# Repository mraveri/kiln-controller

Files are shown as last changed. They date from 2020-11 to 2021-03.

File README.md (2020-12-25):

Kiln Controller
==========

Turns a Raspberry Pi into an inexpensive, web-enabled kiln controller.

## Features

  * easy to create new kiln schedules and edit / modify existing schedules
  * no limit to runtime - fire for days if you want
  * view status from multiple devices at once - computer, tablet etc
  * firing cost estimate
  * NIST-linearized conversion for accurate K type thermocouple readings
  * supports PID parameters you tune to your kiln
  * monitors temperature in kiln after schedule has ended
  * api for starting and stopping at any point in a schedule

**Run Kiln Schedule**



**Edit Kiln Schedule**



## Hardware

### Parts

| Image | Hardware | Description |
| ---| --- | --- |
|  | [Raspberry Pi](https://www.adafruit.com/category/105) | Virtually any Raspberry Pi will work since only a few GPIO pins are being used. |
|  | [MAX 31855](https://www.adafruit.com/product/269) | Thermocouple breakout board |
|  | [K-Type Thermocouple](https://www.auberins.com/index.php?main_page=product_info&cPath=20_3&products_id=39) | Invest in a heavy duty, ceramic, k-type thermocouple designed for kilns |
|  | Breadboard | breadboard, ribbon cable, connector for pi's gpio pins & connecting wires |
|  | Solid State Relay | Zero crossing, make sure it can handle the max current of your kiln. Even if the kiln is 220V you can buy a single [3 Phase SSR](https://www.auberins.com/index.php?main_page=product_info&cPath=2_30&products_id=331). It's like having 3 SSRs in one.  Relays this big always require a heat sink. |
|  | Electric Kiln | There are many old electric kilns on the market that don't have digital controls. You can pick one up on the used market cheaply.  This controller will work with 110V or 220V (pick a proper SSR). My kiln is a Skutt KS-1018. |

### Schematic

The pi has three gpio pins connected to the MAX31855 chip. D0 is configured as an input and CS and CLK are outputs. The signal that controls the solid state relay starts as a gpio output which drives a transistor acting as a switch in front of it. This transistor provides 5V and plenty of current to control the ssr. Since only four gpio pins are in use, any pi can be used for this project. See the [config](https://github.com/jbruce12000/kiln-controller/blob/master/config.py) file for gpio pin configuration.

My controller plugs into the wall, and the kiln plugs into the controller.

**WARNING** This project involves high voltages and high currents. Please make sure that anything you build conforms to local electrical codes and aligns with industry best practices.



*Note: I tried to power my ssr directly using a gpio pin, but it did not work. My ssr required 25ma to switch and rpi's gpio could only provide 16ma. YMMV.*

## Software

### Raspbian

Download [NOOBs](https://www.raspberrypi.org/downloads/noobs/). Copy files to an SD card. Install raspbian on RPi using NOOBs.

    $ sudo apt-get install python3-pip python3-dev python3-virtualenv libevent-dev virtualenv
    $ git clone https://github.com/jbruce12000/kiln-controller.git
    $ cd kiln-controller
    $ virtualenv -p python3 venv
    $ source venv/bin/activate
    $ pip install --upgrade setuptools
    $ pip install greenlet bottle gevent gevent-websocket

*Note: The above steps work on ubuntu if you prefer*

### Raspberry PI deployment

If you want to deploy the code on a PI for production:

    $ cd kiln-controller
    $ virtualenv -p python3 venv
    $ source venv/bin/activate
    $ pip install RPi.GPIO

If you also want to use the in-kernel SPI drivers with a MAX31855 sensor:

    $ sudo apt-get install python-dev
    $ pip install Adafruit-MAX31855

## Configuration

All parameters are defined in config.py, just copy the example and review/change to your mind's content.

    $ cp config.py.EXAMPLE config.py

You should change, test, and verify PID parameters in config.py.  Here is a [PID Tuning Guide](https://github.com/jbruce12000/kiln-controller/blob/master/docs/pid_tuning.md).

You may want to change the configuration parameter **sensor_time_wait**. It's the duty cycle for the entire system.  It's set to two seconds by default which means that a decision is made every 2s about whether to turn on relay[s] and for how long. If you use mechanical relays, you may want to increase this. At 2s, my SSR switches 11,000 times in 13 hours.

## Usage

### Server Startup

    $ source venv/bin/activate; ./kiln-controller.py

### Autostart Server onBoot
If you want the server to autostart on boot, run the following commands

    $ /home/pi/kiln-controller/start-on-boot

### Client Access

Click http://127.0.0.1:8081 for local development or the IP
of your PI and the port defined in config.py (default 8081).

### Simulation

Select a profile and click Start. If you do not have a raspberry pi connected
and configured, then your run will be simulated.  Simulations run at near real
time and kiln characteristics are defined in config.py.

## License

This program is free software: you can redistribute it and/or modify
it under the terms of the GNU General Public License as published by
the Free Software Foundation, either version 3 of the License, or
(at your option) any later version.

This program is distributed in the hope that it will be useful,
but WITHOUT ANY WARRANTY; without even the implied warranty of
MERCHANTABILITY or FITNESS FOR A PARTICULAR PURPOSE.  See the
GNU General Public License for more details.

You should have received a copy of the GNU General Public License
along with this program.  If not, see <http://www.gnu.org/licenses/>.

## Support & Contact

Please use the issue tracker for project related issues.
If you're having trouble with hardware, I did too.  Here is a [troubleshooting guide](https://github.com/jbruce12000/kiln-controller/blob/master/docs/troubleshooting.md) I created for testing RPi gpio pins.

## Origin
This project was originally forked from https://github.com/apollo-ng/picoReflow but has diverged a large amount.

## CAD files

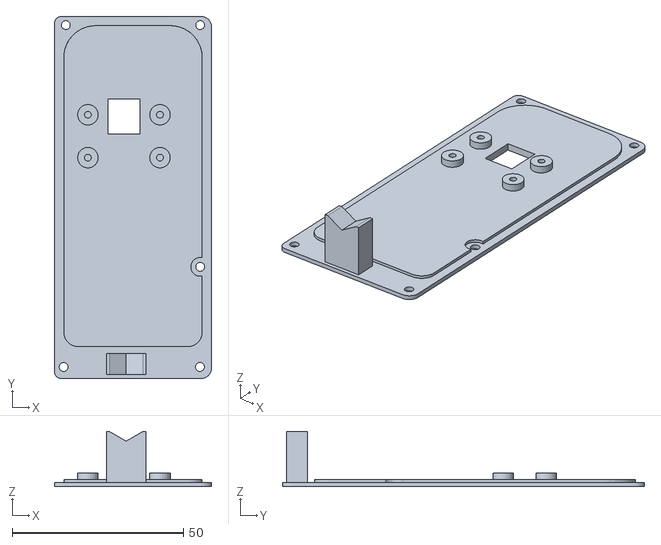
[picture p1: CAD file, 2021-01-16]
3d_model/box A.stl
45.8 x 105.7 x 16.1

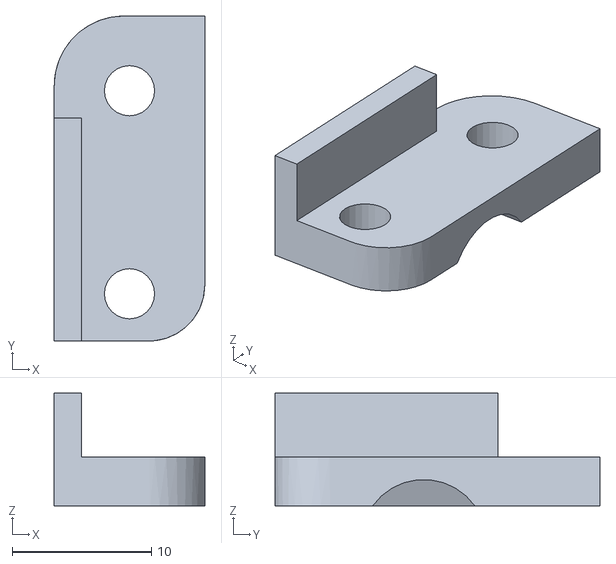
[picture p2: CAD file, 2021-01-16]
3d_model/box C.stl
10.8 x 23.3 x 8.09

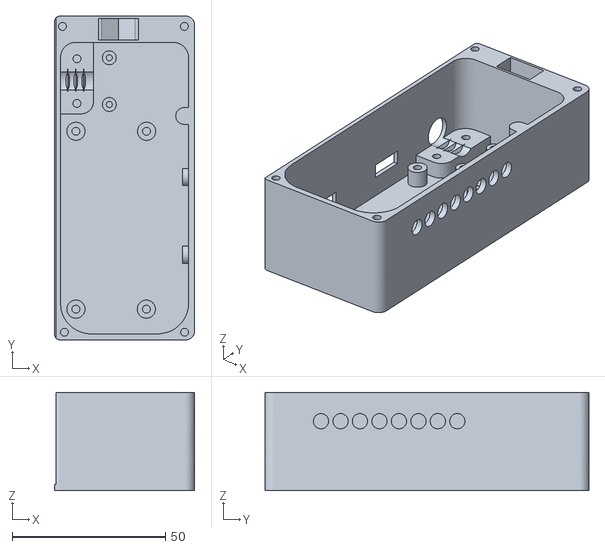
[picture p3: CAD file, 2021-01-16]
3d_model/box B.stl
45.8 x 105.7 x 32.0

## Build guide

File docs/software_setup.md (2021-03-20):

Kiln Monitor Software Set-up
============================

These instructions work for a headless set up that requires no external monitor but intensive command line work. It should be possible to do most of this with a monitor as well but I have not tried.

## General set-up

This part takes care of setting up the Raspberry and the OS. Each of this steps should have infinite tutorials online if needed.

In particular I use mac-os and I'll write commands for that. This should be morally similar for linux but definitely not for windows.

Main reference is this page:

    https://www.raspberrypi.org/documentation/configuration/wireless/headless.md

Start by burning the Raspbian image to an SD card.

    https://www.raspberrypi.org/software/

I use the Raspberry Pi OS (32 bits) other options might work as well.

After this is done we have to go to the SD card and mingle with it a bit.
Most of this material can be found looking online for a headless set up of the raspberry pi tutorial.
Go to the drive that was just installed (you might need to remove the SD and pop it in again).

    cd /Volumes/boot/

Then give the following command to enable ssh login:

    touch ssh

Then instruct the pi to connect to the wifi:

    touch wpa_supplicant.conf

This file contains the connection details that the pi will use.
Edit the wpa_supplicant.conf file following the instructions at:

    https://www.raspberrypi.org/documentation/configuration/wireless/headless.md
    https://www.raspberrypi.org/documentation/configuration/wireless/wireless-cli.md

Add all your wi-fi connections, as an example in my case my home wi-fi and studio wi-fi. My file looks something like this:

    ctrl_interface=DIR=/var/run/wpa_supplicant GROUP=netdev
    update_config=1
    country=US

    network={
     ssid="name"
     psk="password"
     priority=1
     id_str="home"
    }

    network={
     ssid="name"
     psk="password"
     priority=2
     id_str="studio"
    }

Now the pi is ready to be powered up and configured. Remove the SD card and place it in the pi. Power it up and give it a little time to connect to the wi-fi. Then ssh to the raspberry as:

    ssh pi@raspberrypi.local

and, when prompted, give it the default password:

    raspberry

If you are not able to connect it might mean that the pi and the computer are not in the same network or that the wpa_supplicant.conf file is not properly configured.

Now we run a full system update:

    sudo apt-get update
    sudo apt-get full-upgrade -y

Leave the pi finish, it might take a while.
If connection drops in this stage it is likely that you have to restart the whole installation as a failure in updating likely corrupts the system.

Now we run the config script:

    sudo raspi-config

Navigating the script we make sure that:

1. 3p1 enable the camera
2. 3p4 enable SPI
3. 3p5 enable I2C
4. 5l2 to set the time zone
5. 6a1 to expand partition and use the full SD card

If you want to change the network name of the pi from the default raspberrypi you can edit the file:

    sudo nano /etc/hostname

then change raspberrypi to the name you chose in the file:

    sudo nano /etc/hosts

You should really do this if you plan to expose to the whole internet the monitor.

Now reboot with:

    sudo reboot

Notice that when you want to reconnect you have to use the new hostname.

**Setting up security:**

It is now time to step up the security of the pi. This is a crucial step to the security of the entire system and should not be overlooked.

We are planning to expose the pi to the whole internet so we need to be extra carefull.

We follow the instructions at:

    https://www.raspberrypi.org/documentation/configuration/security.md

Change password, take a note of the password and make it strong.

Then make sudo require a password.

Then we set up an ssh key login that does not require password, like https://www.raspberrypi.org/documentation/remote-access/ssh/passwordless.md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

And we disable the possibility of logging in without the password. This prevents any computer that does not have the key to log in the pi and makes the system far more secure.

## Kiln-Monitor installation

First we download the software from github:

    cd $HOME
    git clone https://github.com/mraveri/kiln-controller.git
    cd kiln-controller

If you want to reinstall the software just remove the kiln-controller folder and restart from here.

Then we use the installation script in the script directory:

    ./script/install_on_pi

This will go on for a while. You can check the script content to see what this is doing.

The installer creates two empty files: mail_credentials.txt and log_credentials.txt

The first file is used to set up email notifications.
Open mail_credentials and fill three lines with the email address that will send emails, the password and its name. I use a dummy gmail account and my credential file looks like this:

    name@gmail.com
    password
    Name Sending Email

The second file is used to protect connecting to the pi web interface.
Open the file and write:

    username
    password

These should definitely be different from your raspberry user and password.
These are not encrypted but should not be accessible from anybody that does
not have access to the physical pi and your computer...

Go to ngrok. Register and authenticate.
Autenticate root with:

    sudo /home/pi/kiln-controller/venv/bin/ngrok authtoken ...

Then reboot the pi.

Now turn on the leds by:

    sudo ./script/light_setup

Now turn on wi-fi management with led by giving:

    sudo ./script/wifi_setup

And since we want the monitor to run at startup we give:

    sudo ./script/start-monitor-on-boot

These are instructions for deployment, if you want to develop the code refer to the
standard instructions.

## LED

Blacklist audio, check if necessary
https://www.raspberrypi.org/forums/viewtopic.php?t=151460

Install all drivers, manually if necessary.

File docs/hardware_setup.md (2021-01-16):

Kiln Monitor Hardware Set-up
============================

To make this minimal electronic soldering capabilities are needed.

## Parts

### Enclosure:

You can pick the enclosure you prefer.
The file (link) contains a 3D model of the one we use and that can be mounted on a camera stand. This has the space to mount all the things that are needed.
The model can be 3D printed relatively easily.

1. Enclosure (3d print model)
2. Screws (list sizes)
3. Camera stand bolt (dimensions?)

### Raspberry and Thermocouple:

These go as in the main readme with the addition of status leds and camera for monitoring.

1. Raspberry pi zero w
2. USB and HDMI adapters for external monitor and keyboard
3. Power adapter for pi
4. SD card fast and 16 Gb
5. Heat sink
6. Camera module
7. Thermocouple amplifier
8. Thermocouple and thermocouple cable
9. Led module NeoPixel Stick
10. misc cables to solder

### Other things you might need:

But not necessarily.

1. Electronic soldering equipment
2. Screwdrivers of different sizes (most noticeably M1, M2, M3 that are less common)
3. 3D printer for enclosure
4. a wi-fi connection (although probably not really necessary)

## Mounting

Screws:

1. 4 x M2*4 for camera
2. 5 x M3*6 for cover
3. 4 x M2.6*6 for Raspberry
4. 2 x M2.6*8 for thermocouple cable
5. 2 x M2*6 for thermocouple amplifier

Soldering work

Thermocouple reader to GPIO

### External LED:

Connect the wiring, connect both grounds.
connect power to second 3v3 port.

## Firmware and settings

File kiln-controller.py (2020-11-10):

#!/usr/bin/env python

import os
import sys
import logging
import json

import bottle
import gevent
import geventwebsocket
#from bottle import post, get
from gevent.pywsgi import WSGIServer
from geventwebsocket.handler import WebSocketHandler


try:
    sys.dont_write_bytecode = True
    import config
    sys.dont_write_bytecode = False
except:
    print ("Could not import config file.")
    print ("Copy config.py.EXAMPLE to config.py and adapt it for your setup.")
    exit(1)

logging.basicConfig(level=config.log_level, format=config.log_format)
log = logging.getLogger("kiln-controller")
log.info("Starting kill controller")

script_dir = os.path.dirname(os.path.realpath(__file__))
sys.path.insert(0, script_dir + '/lib/')
profile_path = os.path.join(script_dir, "storage", "profiles")

from oven import Oven, Profile
from ovenWatcher import OvenWatcher

app = bottle.Bottle()
oven = Oven()
ovenWatcher = OvenWatcher(oven)

@app.route('/')
def index():
    return bottle.redirect('/picoreflow/index.html')

@app.post('/api')
def handle_api():
    log.info("/api is alive")
    log.info(bottle.request.json)

    # run a kiln schedule
    if bottle.request.json['cmd'] == 'run':
        wanted = bottle.request.json['profile']
        log.info('api requested run of profile = %s' % wanted)

        # start at a specific minute in the schedule
        # for restarting and skipping over early parts of a schedule
        startat = 0;
        if 'startat' in bottle.request.json:
            startat = bottle.request.json['startat']

        # get the wanted profile/kiln schedule
        profile = find_profile(wanted)
        if profile is None:
            return { "success" : False, "error" : "profile %s not found" % wanted }

        # FIXME juggling of json should happen in the Profile class
        profile_json = json.dumps(profile)
        profile = Profile(profile_json)
        oven.run_profile(profile,startat=startat)
        ovenWatcher.record(profile)

    if bottle.request.json['cmd'] == 'stop':
        log.info("api stop command received")
        oven.abort_run()

    return { "success" : True }

def find_profile(wanted):
    '''
    given a wanted profile name, find it and return the parsed
    json profile object or None.
    '''
    #load all profiles from disk
    profiles = get_profiles()
    json_profiles = json.loads(profiles)

    # find the wanted profile
    for profile in json_profiles:
        if profile['name'] == wanted:
            return profile
    return None

@app.route('/picoreflow/:filename#.*#')
def send_static(filename):
    log.debug("serving %s" % filename)
    return bottle.static_file(filename, root=os.path.join(os.path.dirname(os.path.realpath(sys.argv[0])), "public"))


def get_websocket_from_request():
    env = bottle.request.environ
    wsock = env.get('wsgi.websocket')
    if not wsock:
        abort(400, 'Expected WebSocket request.')
    return wsock


@app.route('/control')
def handle_control():
    wsock = get_websocket_from_request()
    log.info("websocket (control) opened")
    while True:
        try:
            message = wsock.receive()
            log.info("Received (control): %s" % message)
            msgdict = json.loads(message)
            if msgdict.get("cmd") == "RUN":
                log.info("RUN command received")
                profile_obj = msgdict.get('profile')
                if profile_obj:
                    profile_json = json.dumps(profile_obj)
                    profile = Profile(profile_json)
                oven.run_profile(profile)
                ovenWatcher.record(profile)
            elif msgdict.get("cmd") == "SIMULATE":
                log.info("SIMULATE command received")
                #profile_obj = msgdict.get('profile')
                #if profile_obj:
                #    profile_json = json.dumps(profile_obj)
                #    profile = Profile(profile_json)
                #simulated_oven = Oven(simulate=True, time_step=0.05)
                #simulation_watcher = OvenWatcher(simulated_oven)
                #simulation_watcher.add_observer(wsock)
                #simulated_oven.run_profile(profile)
                #simulation_watcher.record(profile)
            elif msgdict.get("cmd") == "STOP":
                log.info("Stop command received")
                oven.abort_run()
        except WebSocketError:
            break
    log.info("websocket (control) closed")


@app.route('/storage')
def handle_storage():
    wsock = get_websocket_from_request()
    log.info("websocket (storage) opened")
    while True:
        try:
            message = wsock.receive()
            if not message:
                break
            log.debug("websocket (storage) received: %s" % message)

            try:
                msgdict = json.loads(message)
            except:
                msgdict = {}

            if message == "GET":
                log.info("GET command received")
                wsock.send(get_profiles())
            elif msgdict.get("cmd") == "DELETE":
                log.info("DELETE command received")
                profile_obj = msgdict.get('profile')
                if delete_profile(profile_obj):
                  msgdict["resp"] = "OK"
                wsock.send(json.dumps(msgdict))
                #wsock.send(get_profiles())
            elif msgdict.get("cmd") == "PUT":
                log.info("PUT command received")
                profile_obj = msgdict.get('profile')
                #force = msgdict.get('force', False)
                force = True
                if profile_obj:
                    #del msgdict["cmd"]
                    if save_profile(profile_obj, force):
                        msgdict["resp"] = "OK"
                    else:
                        msgdict["resp"] = "FAIL"
                    log.debug("websocket (storage) sent: %s" % message)

                    wsock.send(json.dumps(msgdict))
                    wsock.send(get_profiles())
        except WebSocketError:
            break
    log.info("websocket (storage) closed")


@app.route('/config')
def handle_config():
    wsock = get_websocket_from_request()
    log.info("websocket (config) opened")
    while True:
        try:
            message = wsock.receive()
            wsock.send(get_config())
        except WebSocketError:
            break
    log.info("websocket (config) closed")


@app.route('/status')
def handle_status():
    wsock = get_websocket_from_request()
    ovenWatcher.add_observer(wsock)
    log.info("websocket (status) opened")
    while True:
        try:
            message = wsock.receive()
            wsock.send("Your message was: %r" % message)
        except WebSocketError:
            break
    log.info("websocket (status) closed")


def get_profiles():
    try:
        profile_files = os.listdir(profile_path)
    except:
        profile_files = []
    profiles = []
    for filename in profile_files:
        with open(os.path.join(profile_path, filename), 'r') as f:
            profiles.append(json.load(f))
    return json.dumps(profiles)


def save_profile(profile, force=False):
    profile_json = json.dumps(profile)
    filename = profile['name']+".json"
    filepath = os.path.join(profile_path, filename)
    if not force and os.path.exists(filepath):
        log.error("Could not write, %s already exists" % filepath)
        return False
    with open(filepath, 'w+') as f:
        f.write(profile_json)
        f.close()
    log.info("Wrote %s" % filepath)
    return True

def delete_profile(profile):
    profile_json = json.dumps(profile)
    filename = profile['name']+".json"
    filepath = os.path.join(profile_path, filename)
    os.remove(filepath)
    log.info("Deleted %s" % filepath)
    return True


def get_config():
    return json.dumps({"temp_scale": config.temp_scale,
        "time_scale_slope": config.time_scale_slope,
        "time_scale_profile": config.time_scale_profile,
        "kwh_rate": config.kwh_rate,
        "currency_type": config.currency_type})


def main():
    ip = config.listening_ip
    port = config.listening_port
    log.info("listening on %s:%d" % (ip, port))

    server = WSGIServer((ip, port), app,
                        handler_class=WebSocketHandler)
    server.serve_forever()


if __name__ == "__main__":
    main()

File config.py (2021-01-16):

import logging
import os
import lib.utilities as utilities

########################################################################
#
#   General options

# Logging
log_level = logging.INFO
log_format = '%(asctime)s %(levelname)s %(name)s: %(message)s'

# Server
listening_ip = "0.0.0.0"
listening_port = 8081

# Cost Estimate
kwh_rate = 0.18  # Rate in currency_type to calculate cost to run job
currency_type = "$"   # Currency Symbol to show when calculating cost to run job

########################################################################
#
#   GPIO Setup (BCM SoC Numbering Schema)
#
#   Check the RasPi docs to see where these GPIOs are
#   connected on the P1 header for your board type/rev.
#   These were tested on a Pi B Rev2 but of course you
#   can use whichever GPIO you prefer/have available.

# Outputs
gpio_heat = 23  # Switches zero-cross solid-state-relay
heater_invert = 0  # Switches the polarity of the heater control

### Thermocouple Adapter selection:
#   max31855 - bitbang SPI interface
#   max31855spi - kernel SPI interface
#   max6675 - bitbang SPI interface
max31855 = 1
max6675 = 0
max31855spi = 0 # if you use this one, you MUST reassign the default GPIO pins

### Thermocouple Connection (using bitbang interfaces)
gpio_sensor_cs = 27
gpio_sensor_clock = 22
gpio_sensor_data = 17

### Thermocouple SPI Connection (using adafrut drivers + kernel SPI interface)
spi_sensor_chip_id = 0

### duty cycle of the entire system in seconds. Every N seconds a decision
### is made about switching the relay[s] on & off and for how long.
### The thermocouple is read five times during this period and the highest
### value is used.
sensor_time_wait = 2

########################################################################
#
#   PID parameters

pid_kp = 25  # Proportional
pid_ki = 1088  # Integration
pid_kd = 217  # Derivative was 217

########################################################################
#
#   Temperature reading led:

led_controller = "http://0.0.0.0:5001"
temperature_led = 2

########################################################################
#
#   Simulation parameters

sim_t_env = 25.0  # deg C
sim_c_heat = 100.0  # J/K  heat capacity of heat element
sim_c_oven = 5000.0  # J/K  heat capacity of oven
sim_p_heat = 5450.0  # W    heating power of oven
sim_R_o_nocool = 1.0  # K/W  thermal resistance oven -> environment
sim_R_o_cool = 0.05  # K/W  " with cooling
sim_R_ho_noair = 0.1  # K/W  thermal resistance heat element -> oven
sim_R_ho_air = 0.05  # K/W  " with internal air circulation

########################################################################
#
#   Time and Temperature parameters

temp_scale = "f"  # c = Celsius | f = Fahrenheit - Unit to display
time_scale_slope = "h"  # s = Seconds | m = Minutes | h = Hours - Slope displayed in temp_scale per time_scale_slope
time_scale_profile = "m"  # s = Seconds | m = Minutes | h = Hours - Enter and view target time in time_scale_profile

# emergency shutoff the kiln if this temp is reached.
# when solid state relays fail, they usually fail closed.  this means your
# kiln receives full power until your house burns down.
# this should not replace you watching your kiln or use of a kiln-sitter
emergency_shutoff_temp = 2250

# not used yet
# if measured value is N degrees below set point
warning_temp_low = 5

# not used yet
# if measured value is N degrees above set point
warning_temp_high = 5

# thermocouple offset
# If you put your thermocouple in ice water and it reads 36F, you can
# set set this offset to -4 to compensate.  This probably means you have a
# cheap thermocouple.  Invest in a better thermocouple.
thermocouple_offset = 0

########################################################################
#
#   Analysis settings:

# smoothing scale for plots, in hours. Default is 1 minute
smoothing_scale = 1./60.
# cool temperature:
unload_temperature = 122.  # F for 50 C
# zoom around peak for plots:
peak_zoom = 300.

########################################################################
#
#   Authentication and email settings:

here = os.path.dirname(os.path.abspath(__file__))
log = logging.getLogger(__name__)


def helper_error_logging():
    log.critical('Error with authentication file. \n'
                 + 'Create the file: '+here+'/log_credentials.txt \n'
                 + 'With your choice of username and password to log to the kiln monitor \n'
                 + 'First line should be the desired username \n'
                 + 'Second line should be desired password'
                 )
    raise ValueError
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

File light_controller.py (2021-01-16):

###############################################################################
# Initial imports:
###############################################################################

from flask import Flask, request, jsonify
from waitress import serve
import board
import neopixel
import time

###############################################################################
# Settings:
###############################################################################

num_leds = 8
neopixel_gpio_pin = board.D18
neopixel_brightness = 0.2
host = "0.0.0.0"
port = 5001

###############################################################################
# Predefined colors:
###############################################################################

RED = (255, 0, 0)
YELLOW = (255, 150, 0)
GREEN = (0, 255, 0)
CYAN = (0, 255, 255)
BLUE = (0, 0, 255)
PURPLE = (180, 0, 255)

###############################################################################
# Effects:
###############################################################################


def wheel(pos):
    # Input a value 0 to 255 to get a color value.
    # The colours are a transition r - g - b - back to r.
    if pos < 0 or pos > 255:
        return (0, 0, 0)
    if pos < 85:
        return (255 - pos * 3, pos * 3, 0)
    if pos < 170:
        pos -= 85
        return (0, 255 - pos * 3, pos * 3)
    pos -= 170
    return (pos * 3, 0, 255 - pos * 3)


def color_chase(color, wait, pixels):
    for i in range(num_leds):
        pixels[i] = color
        time.sleep(wait)
        pixels.show()
    time.sleep(0.5)


def rainbow_cycle(wait, pixels):
    for j in range(255):
        for i in range(num_leds):
            rc_index = (i * 256 // num_leds) + j
            pixels[i] = wheel(rc_index & 255)
        pixels.show()
        time.sleep(wait)

###############################################################################
# Main app:
###############################################################################


def main():

    # initialize server:
    app = Flask(__name__)

    # initialize pixels:
    pixels = neopixel.NeoPixel(neopixel_gpio_pin,
                               num_leds,
                               brightness=neopixel_brightness)
    pixels.fill((0, 0, 0))

    # some initial fireworks:
    pixels.fill((0, 0, 0))
    color_chase(RED, 0.01, pixels)
    color_chase(YELLOW, 0.01, pixels)
    color_chase(GREEN, 0.01, pixels)
    color_chase(CYAN, 0.01, pixels)
    color_chase(BLUE, 0.01, pixels)
    color_chase(PURPLE, 0.01, pixels)
    rainbow_cycle(0, pixels)
    pixels.fill((0, 0, 0))
    pixels[0] = GREEN

    @app.route('/', methods=['POST'])
    def color_pixels():

        if request.method == 'POST':
            command = request.get_json()
            # execute effects first:
            for key in command.keys():
                if key == 'color_chase':
                    color_chase(command['color_chase'][0], command['color_chase'][1], pixels)
                elif key == 'rainbow_cycle':
                    rainbow_cycle(command['rainbow_cycle'], pixels)
                elif key == 'fill':
                    pixels.fill(command[key])
                elif key == 'brightness':
                    pixels.brightness = command[key]
            # set colors as instructed:
            for key in command.keys():
                try:
                    ind = int(key)
                    pixels[ind] = command[key]
                except ValueError:
                    pass
            # get state:
            state = {}
            for ind, pix in enumerate(pixels):
                state[ind] = list(list(pix))
            #
            return jsonify(state), 200

    serve(app, host=host, port=port)


if __name__ == '__main__':
    main()

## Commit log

2020-11-21 Added monitor material
2021-01-05 Small add
    [box_A.stl, box_B.stl, box_C.stl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]
2021-01-16 Added stuff
    [box A.stl, box B.stl, box C.stl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]
